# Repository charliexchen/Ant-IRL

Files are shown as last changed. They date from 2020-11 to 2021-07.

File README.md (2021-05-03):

# Ant-IRL

Ant-v2 (A.K.A Antony) is now a fairly standard RL task from the Open AI gym library. This project aims to achieve three goals:
* Build a physical robot in a similar configuration to Ant-v2
* Train Actor Critic on a physical environment with no simulation
* Use Haiku with JAX (https://github.com/deepmind/dm-haiku) on an end to end project

...in addition to staying sane over the third lock down in the UK.
 <p align="center">
   
 </p>
<p align="center"><i> <sub>Improvements in the robot's speed after training with AAC with experience replay in the simplified environment. Left: pretrained agent with some random noise in actions. Middle: agent after optimising for 33 episodes. Right: agent after optimising for 91 episodes</sub></i> </p>

## Building the Robot

<p align="center">
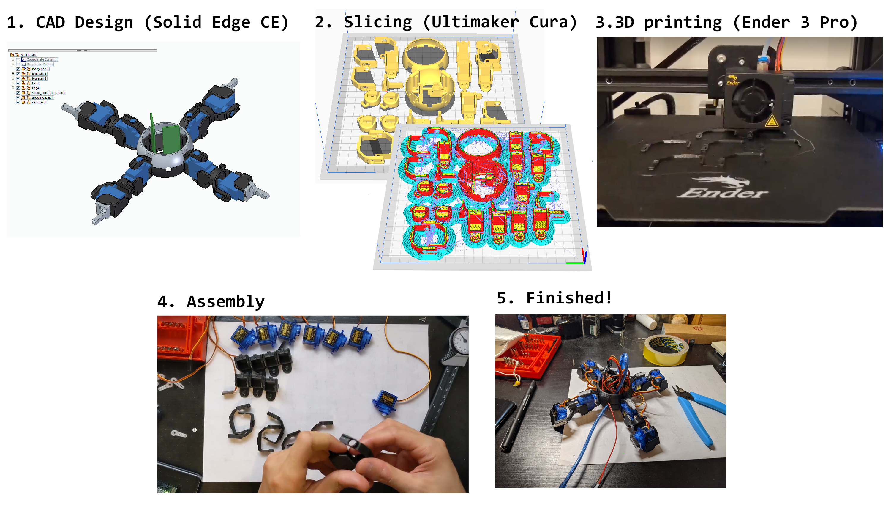
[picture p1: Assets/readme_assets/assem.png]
   
</p>

First, the robot was designed using Siemens Solid Edge CE (a powerful but free CAD software) and then 3D printed using my Creality Ender 3. The design consists of 8 servos in a similar configuration to Ant-v2 (albeit the forelegs are shorter to reduce the load on the tiny 9g servos). For control, I used an Arduino Nano which communicates with my desktop via USB serial and the servo controller via i2c. The position of each servo can be manipulated by sending two bytes of data.

For sensing, the Arduino is also connected to a gyro/accelerometer via i2c, which gives us acceleration, the gravity vector and Euler angles. Using the MPU-6050 sensor board's onboard DMP feature, it is not necessary to implement further noise reduction (such as Kalman/complement filters) for the sensors. Unfortunately, I eventually had to discard this data since it was just wasn't that helpful for my robot.

As a future upgrade, I have designed micro switch holders for the forelegs which will allow the robot to know if the legs have contacted the ground.

The robot runs on a 5v 2A DC power supply. Power and USB connection is maintained using 6 thin enamelled copper wires (usually used for electromagnets). This minimises any forces a stiff USB/power cable might impart onto the robot.

## Location Detection

The Robot's location and orientation relative to the environment is detected via the large aruco marker on top of the robot and markers on the corners of the environment. This was achieved with the aruco module in OpenCV. Under the correct lighting conditions, we can have the location of the robot over 99% of the time, and we can resort to last frame position or interpolating for any missing frames.

<p align="center">
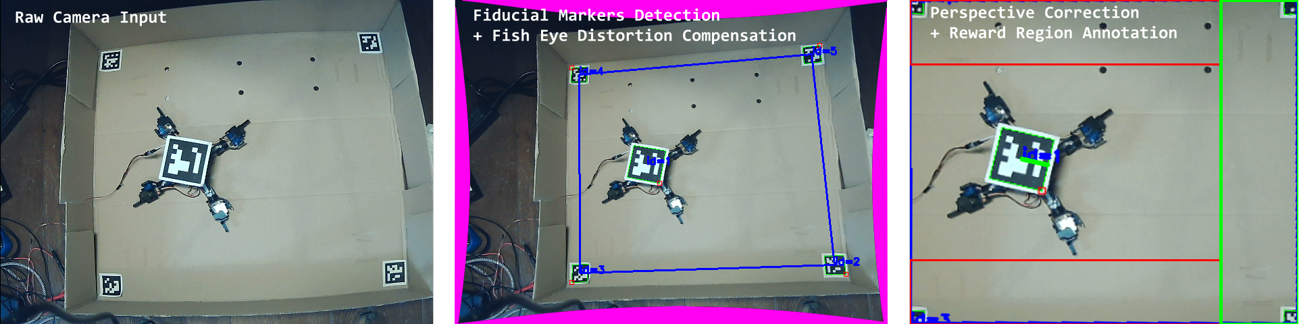
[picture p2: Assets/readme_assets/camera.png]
   
</p>
<p align="center"><i> <sub>Using OpenCV to correct the raw webcam input. Note the small amount of parallax if the camera is not directly overhead. This is usually small enough to not affect the results.</sub></i></p>

The capture setup consists of a cheap webcam on an angled tripod, pointing downwards. With the locations of the corners of the environment known, perspective and fisheye distortion can be corrected with standard OpenCV operations.

<p align="center">
  
</p>
<p align="center"><i> <sub>Camera setup and simple walk. Note the trailing wire connected to power and USB.</sub></i></p>

## Building an Environment

With the above setup, we can implement a state-action-reward loop, which forms the basis of the MDP. The robot would walk forth, collect data, train on that data using one's RL algorithm of choice, before resetting. 

* State consists of sensor inputs, absolute position, orientation, servo positions, creating a 22-dimensional vector (The simplified version of the environment removes sensor inputs, reducing the dimensionality to 12)
* Actions are 8 dimensional vectors representing either new absolute servo positions or deltas between the current position to the next.
* Reward is based on position, with +2 if it reaches the end of the field, -1 if it goes too far off the side and up to 1 for moving from left to right. The simplfied version of the envionment has the velocity dotted with the normalised orientation vector as the reward (essentially the forward speed).

A hand engineered walk cycle is also implemented. This was done for three reasons:
* Given a target and the robot's position, you can let the robot move up/down/left/right until it reached the target. This gives us a reliable method of resetting the robot's position after running an episode.
* We can collect data on this fixed walk cycle (in particular accelerometer/gyro data) in order to pretrain policiy/value functions.
* This makes room for lots of fun, future, non deep-learning projects. I can simply map the commands to keyboard/some other controller, and we basically have a walker which can reliably move in any direction.

<p align="center">
  
</p>
<p align="center"><i> <sub>Walking to specified locations by combining the camera and the hand engineered gait. This is used to reset the environment.</sub></i></p>

## Implementing and Running AAC

I implemented Advantage Actor-Critic using JAX and Haiku. This was a fun framework to use since it is a lot more flexible compared to the others I've tried in the past, such as Keras. Almost any numpy operation can be accelerated, vectorised or differentiated, so I can see this handling more unconventional architectures much more gracefully, even though the overall feature gap isn't huge compared to other frameworks. For example, I especially liked how for autograd, we use grad which is treated like a function operator much like how gradients are represented mathematically.

I made the predictor and AAC class as generic as possible for future projects, and tested that it works on CartPole.

Since this is a physical environment with one agent, we are very data constrained. As such, I first ran a number of episodes using the fixed walk cycle. We collect this data and then use it to pretrain the value function and an actor based on a fixed gait. We then use the above AAC implementation along with experience replay to improve the agent. The initial data also allows for some hyperparameter selection, which was done with a simple random search. 

 <p align="center">
     
 </p>
<p align="center"><i> <sub>Running multiple episodes with fixed agent in the environment to collect training data. Red rectangles terminate with negative reward, green with positive reward. After an episode, the agent returns to the red circle to reset the environment. Note the aruco markers used to ensure consistent perspective in the corners of the environment. </sub></i> </p>

Other things to note about the AAC implementation:
* The environment runs at 30fps (bounded by the frame rate of the camera). This can be downsampled by simply issuing a new action only every x frames. This can give the NNs a longer effective time horizon, in addition to making the setup less sensitive to latency in the camera, sensors and servo controller.
* The problem can be further simplified by imposing symmetries into the robot's actor, though this does remove the robot's ability to turn.
* In order to learn a continuous action space, the actor simply returns the mean values of a normal distribution. The variance is fixed for exploration, but it can also be the output of the actor.

<p float="left" align="center">
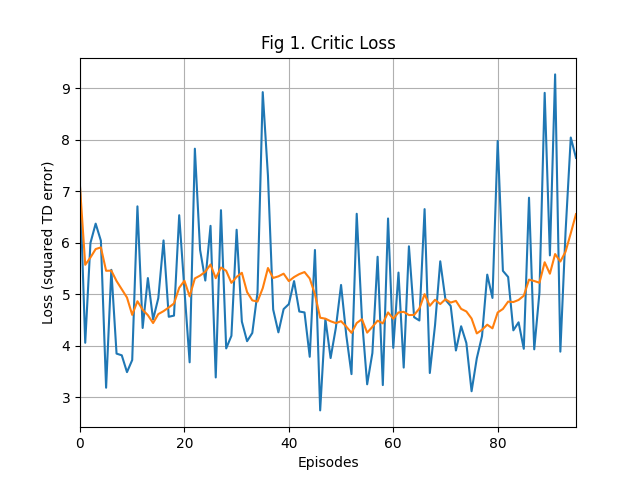
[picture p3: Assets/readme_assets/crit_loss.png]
  
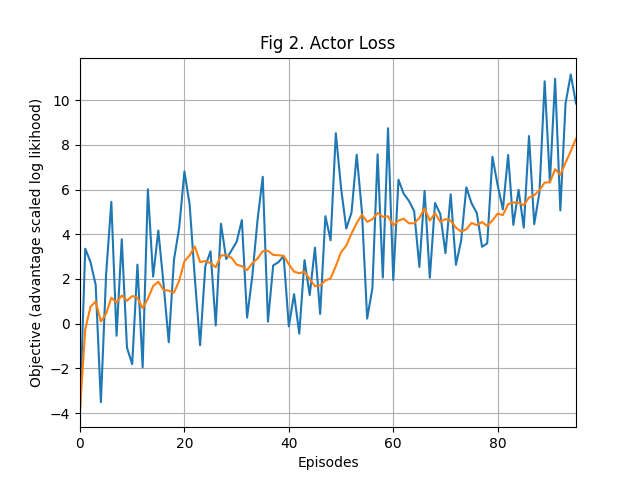
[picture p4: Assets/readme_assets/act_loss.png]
 
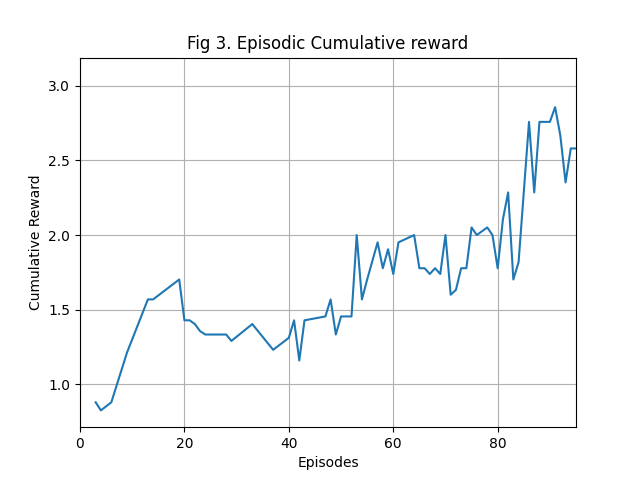
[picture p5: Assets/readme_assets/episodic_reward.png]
 
</p>
<p align="center"><i> <sub>Fig 1: loss function at each episode of the value critic. Given AAC is on-policy, we can expect this value to not go down as long as the policy has not converged. Fig 2: objective of the actor policy. This is the log-likelihood scaled advantage, and so we expect it to go up as the agent improves. Fig 3: Episodic cumulative reward -- the agent is moving faster as the policy improves.</sub></i> </p>

Tuning RL algorithms is hard. To make my life easier, I followed the best some best practices:
* Normalise the input and ouput of the NNs so the values across the layers are of similar magnitude
* Offline training/hyperparameter tuning uses train/dev/test sets to prevent overfitting
* Experiment configurations are separated into config files
* End to end tests for all major components in order to ensure correctness

## References
Main papers I consulted:
* [Challenges of Real-World Reinforcement Learning](https://arxiv.org/abs/1904.12901) -- This is a deepmind paper which gave a high level overview of the kind of problems I'm going to encounter, and served as a good jumping off point.
* [Automated DeepReinforcement Learning Environment for Hardware of a Modular Legged Robot](https://ieeexplore.ieee.org/document/8442201) -- A Disney research paper on getting various configurations to walk using DDPG and TRPO on a modular walking robot. Pretty cool, and gave me an idea about possible RL algorithm candidates. This paper actually trained the agent starting with one leg and increasing the number as legs as you go.
* [Optimizing walking of a humanoid robot using reinforcement learning](https://www.researchgate.net/publication/267024754_Reinforcement_Learning_with_Experience_Replay_for_Model-Free_Humanoid_Walking_Optimization) -- A masters thesis from university of warsaw using AAC. My architecture ended up being pretty similar to this one.
* [RealAnt: An Open-Source Low-Cost Quadruped for Research in Real-World Reinforcement Learning](https://arxiv.org/abs/2011.03085) -- A paper which also builds a open source robot, and trains some gaits on it. This was published days after I had done most of CAD work, so that was a little annoying. However, this design used much more expensive servos (each servo cost more than my robot put together) which has inbuilt sensors, superior control and full 360 rotation, and I think that might be worth investing in...
## Parts List
* [WebCam](https://www.amazon.co.uk/gp/product/B08CXV11MX/ref=ppx_yo_dt_b_asin_title_o00_s00?ie=UTF8&psc=1) -- Basically any webcam will do, though I ended up using this one side it comes with a standard standard 1/4-20 UNC thread for use on a tripod, in addition to a hinge and ball mount. These features are fairly common in other webcams though, so don't worry about getting the exact one. If you have a good camera which can be directly connected to PC, there's nothing really stopping you from using that -- just make sure that the latency low and you can detect the fiducial markers.
* [Arduino Nano](https://www.amazon.co.uk/ELEGOO-Arduino-board-ATmega328P-compatible/dp/B072BMYZ18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) -- Standard arduino. [There are lots of tutorials online for using these](https://store.arduino.cc/).
* [PCA9685 Servo Controller](https://www.amazon.co.uk/TeOhk-Channel-Interface-Controller-Raspberry/dp/B07RVJRQX1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) -- Interfaces with arduino with i2c and connects to external power.
* [MPU-6050 Sensor Board](https://www.amazon.co.uk/Neuftech%C2%AE-MPU-6050-3-gyroscope-accelerometer-crafting/dp/B00PIMRJX6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) -- Accelerometer, gyro and temperature sensor on a single board which can then communicate with i2c. Gyros are very accurate, but its values need to be integrated in order to get angular position, resulting in drift. Accelerometers don't have problems in drift, but are often really noisy. It is possible to combine data from both sensors in order to get the best of both worlds, and the DMP feature on these boards mean you don't have to write the complement filter yourself. Tutorial on how to get the DMP working can be found [here](https://maker.pro/arduino/tutorial/how-to-interface-arduino-and-the-mpu-6050-sensor), though personally I did discard the data here since it wasn't super helpful.
* [Tower Pro SG90 Servos](https://www.amazon.co.uk/gp/product/B07LBS7WYZ/ref=ppx_yo_dt_b_asin_title_o03_s00?ie=UTF8&psc=1) -- Super cheap 9g servos used in model aircraft. I recommend looking at some more expensive ones with the same dimensions however, since these were pretty imprecise.
* [SUNLU PLA filament](https://www.amazon.co.uk/gp/product/B07TMKGGS3/ref=ppx_yo_dt_b_asin_title_o00_s00?ie=UTF8&psc=1) -- I used this black filament, but PLA is so forgiving a plastic to print it really doesn't matter which brand you use.
* [0.2mm Enamelled copper wire](https://www.ebay.co.uk/itm/143728062658?ssPageName=STRK%3AMEBIDX%3AIT&_trksid=p2060353.m2749.l2649) -- Usually used for making electromagnets. I used this to make a long flexible cable with 6 wires, 4 for USB, and 2 for powering the servos. Some light soldering is needed here.
* [5v 2a power supply](https://www.amazon.co.uk/gp/product/B08DXX6LGG/ref=ppx_yo_dt_b_asin_title_o06_s00?ie=UTF8&psc=1) -- Used to power the servos. You can power one or two servos directly with the arduino, but you'll need an external power supply if you want to power more -- drawing too much current will damage the arduino. Be careful with these -- whilst they're not going to burn your house down, they're surprisingly expensive compared to the rest of the project and will fry themselves if shorted. If you forsee that you're going to be doing a lot of electrionic projects, I recommend getting one of these [variable DC power supplies](https://www.amazon.co.uk/gp/product/B08HQG9D56/ref=ppx_yo_dt_b_asin_title_o02_s00?ie=UTF8&psc=1), since they're much more flexible and is current limited, protecting it against shorts.
<p align="center">
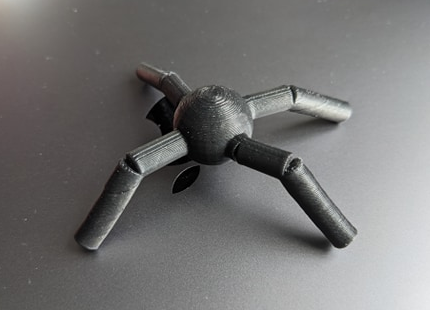
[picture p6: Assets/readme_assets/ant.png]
     
 </p>
 <p align="center"><i> <sub>You've made it to the end! Thank you for reading! </sub></i> </p>

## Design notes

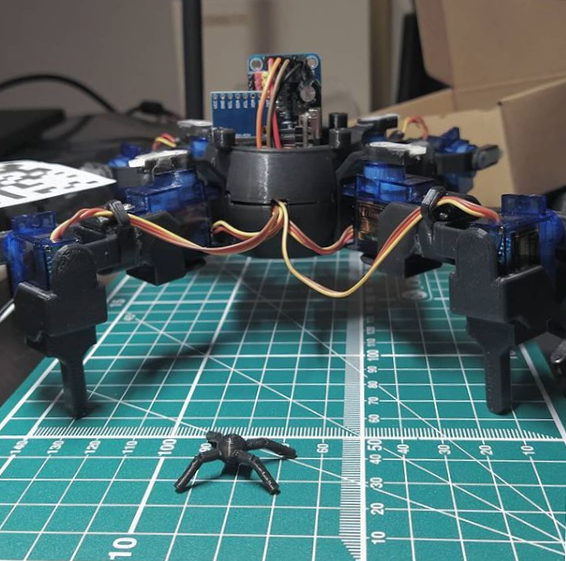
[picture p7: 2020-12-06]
Assets/readme_assets/ant_irl.png

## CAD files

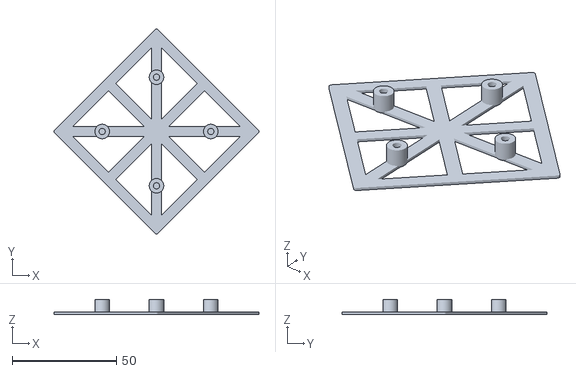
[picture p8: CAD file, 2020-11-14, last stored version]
Parts/qr_holder.stl
98.2 x 98.2 x 7.00

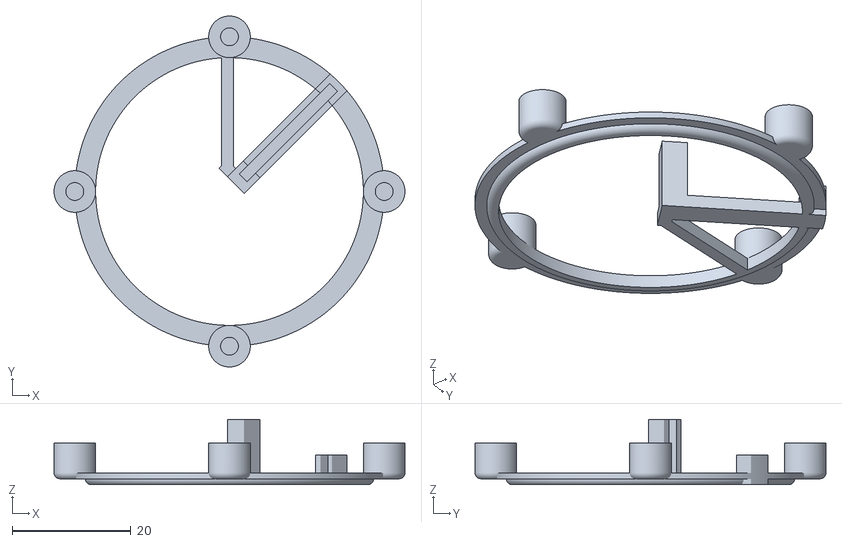
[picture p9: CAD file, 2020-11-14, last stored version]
Parts/modular_holder.stl
59.0 x 59.0 x 11.0

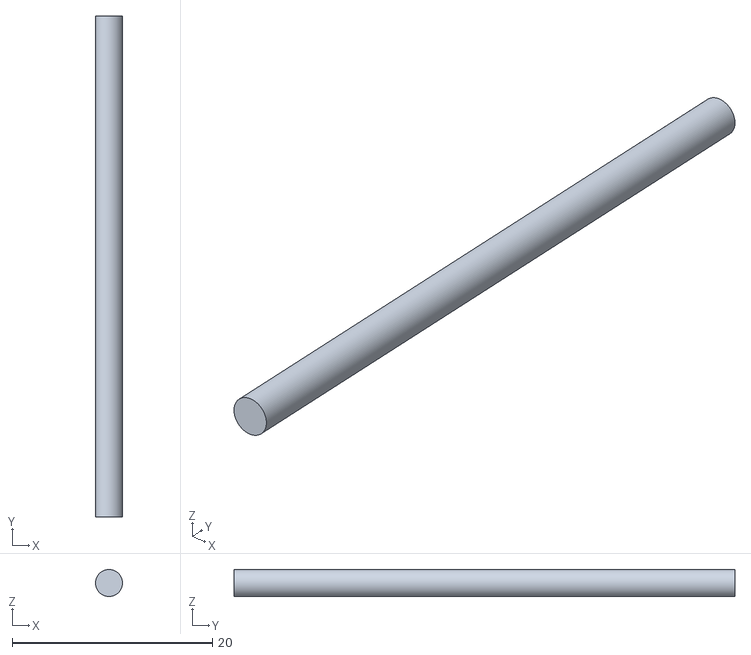
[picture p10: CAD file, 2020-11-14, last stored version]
Parts/rod.stl
2.70 x 50.0 x 2.70

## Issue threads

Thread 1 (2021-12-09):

error opening ant.asm

wegesdal, 2021-12-09:
feet.par, joint.asm, thigh.par missing from assets folder. Is ant.asm based on a previous directory structure? joint.asm and thigh.par have path outside project folder.

charliexchen, 2021-12-09:
Heya -- yeah, I rejigged the file structure a little since it was a little all over the place before and this seems to have broken the .asm files.

I've since moved away from Solid Edge for Fusion 360 on my new desktop, so I can't fix this this at the moment. However,
as a temporary measure but you should be able to use Solid Edge to point the directories to the correct positions.

wegesdal, 2021-12-10:
Sounds good. It looks like joint and thigh are missing from the parts folder unless those have been renamed. The path was to desktop instead of parts folder. I am going to try and put one together. My final project for AI was testing Soft-Actor-Critic in gym and I was interested to build my own Ant.

charliexchen, 2021-12-10:
Ah, I see.

charliexchen, 2021-12-11:
Heya, I'm terribly sorry --  I had a look at my backups today, and I'm afraid that file actually lives on a different computer which I currently don't have access to.

If you really need the part ASAP, thigh.par should be quite easy to design. I've highlighted the part of the robot CAD image it refers to.
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

This part is literally just a cylinder with a rectangular hole on each end. The two holes are perpendicular to eachother. On the bracket.par and outer bracket.par files, there is a rectangle which aligns with these holes as you glue the parts together.

wegesdal, 2021-12-11:
I am using mujoco gym for my project I was going to build the robot to extend my learning so I don't have a deadline.

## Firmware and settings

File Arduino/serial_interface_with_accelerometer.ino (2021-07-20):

#include "I2Cdev.h"
#include "MPU6050_6Axis_MotionApps20.h"
#if I2CDEV_IMPLEMENTATION == I2CDEV_ARDUINO_WIRE
#include "Wire.h"
#endif


#include <Wire.h>
#include <Adafruit_PWMServoDriver.h>


Adafruit_PWMServoDriver pwm = Adafruit_PWMServoDriver();
int incomingByte = 0;    // for incoming serial data
int currentCommands[8] = {1500, 1500, 1500, 1500, 1500, 1500, 1500, 1500}; // initial servo positions
int servoPositionOffset = 8;

int maxPulse = 2400;
int minPulse = 600;

unsigned int raw_command = 0;
#define SERVO_FREQ 50 // Analog servos run at ~50 Hz updates

int granularity = 1;


MPU6050 mpu;

#define INTERRUPT_PIN 2  // use pin 2 on Arduino Uno & most boards
#define LED_PIN 13 // (Arduino is 13, Teensy is 11, Teensy++ is 6)
bool blinkState = false;

// MPU control/status vars
bool dmpReady = false;  // set true if DMP init was successful
uint8_t mpuIntStatus;   // holds actual interrupt status byte from MPU
uint8_t devStatus;      // return status after each device operation (0 = success, !0 = error)
uint16_t packetSize;    // expected DMP packet size (default is 42 bytes)
uint16_t fifoCount;     // count of all bytes currently in FIFO
uint8_t fifoBuffer[64]; // FIFO storage buffer

// orientation/motion vars
Quaternion q;           // [w, x, y, z]         quaternion container
VectorInt16 aa;         // [x, y, z]            accel sensor measurements
VectorInt16 aaReal;     // [x, y, z]            gravity-free accel sensor measurements
VectorInt16 aaWorld;    // [x, y, z]            world-frame accel sensor measurements
VectorFloat gravity;    // [x, y, z]            gravity vector
float euler[3];         // [psi, theta, phi]    Euler angle container
float ypr[3];           // [yaw, pitch, roll]   yaw/pitch/roll container and gravity vector

typedef struct {
  float qw;
  float qx;
  float qy;
  float qz;
  float y;
  float p;
  float r;
  float gx;
  float gy;
  float gz;
  float ed = 99999999.9;
} __attribute__((__packed__))data_packet_t;

data_packet_t dp;

volatile bool mpuInterrupt = false;     // indicates whether MPU interrupt pin has gone high
void dmpDataReady() {
  mpuInterrupt = true;
}

void setup() {

  Serial.begin(9600);    // opens serial port, sets data rate to 9600 bps

  pwm.begin();
  pwm.setOscillatorFrequency(27000000);
  pwm.setPWMFreq(SERVO_FREQ);  // Analog servos run at ~50 Hz updates

  // join I2C bus (I2Cdev library doesn't do this automatically)
#if I2CDEV_IMPLEMENTATION == I2CDEV_ARDUINO_WIRE
  Wire.begin();
  Wire.setClock(400000); // 400kHz I2C clock. Comment this line if having compilation difficulties
#elif I2CDEV_IMPLEMENTATION == I2CDEV_BUILTIN_FASTWIRE
  Fastwire::setup(400, true);
#endif
  while (!Serial); // wait for Leonardo enumeration, others continue immediately
  Serial.println(F("Initializing I2C devices..."));
  mpu.initialize();
  pinMode(INTERRUPT_PIN, INPUT);
  Serial.println(F("Testing device connections..."));
  Serial.println(mpu.testConnection() ? F("MPU6050 connection successful") : F("MPU6050 connection failed"));
  Serial.println(F("Initializing DMP..."));
  devStatus = mpu.dmpInitialize();
  if (devStatus == 0) {
    // Calibration Time: generate offsets and calibrate our MPU6050
    mpu.CalibrateAccel(6);
    mpu.CalibrateGyro(6);
    mpu.PrintActiveOffsets();
    // turn on the DMP, now that it's ready
    Serial.println(F("Enabling DMP..."));
    mpu.setDMPEnabled(true);

    // enable Arduino interrupt detection
    Serial.print(F("Enabling interrupt detection (Arduino external interrupt "));
    Serial.print(digitalPinToInterrupt(INTERRUPT_PIN));
    Serial.println(F(")..."));
    attachInterrupt(digitalPinToInterrupt(INTERRUPT_PIN), dmpDataReady, RISING);
    mpuIntStatus = mpu.getIntStatus();

    // set our DMP Ready flag so the main loop() function knows it's okay to use it
    Serial.println(F("DMP ready! Waiting for first interrupt..."));
    dmpReady = true;

    // get expected DMP packet size for later comparison
    packetSize = mpu.dmpGetFIFOPacketSize();
  } else {
    // ERROR!
    // 1 = initial memory load failed
    // 2 = DMP configuration updates failed
    // (if it's going to break, usually the code will be 1)
    Serial.print(F("DMP Initialization failed (code "));
    Serial.print(devStatus);
    Serial.println(F(")"));
  }

  // configure LED for output
  pinMode(LED_PIN, OUTPUT);
  delay(500);
  Serial.println("Ant Ready!");
   delay(500);
}


void loop() {
  if (Serial.available() > 0) {
    while (Serial.available() > 0) {
      incomingByte = Serial.read();
      raw_command = (raw_command << 7) | (incomingByte & 127);
      bool is_last_bit = (incomingByte & 128) == 128;
      if (is_last_bit) {
        int servo_id = raw_command & 7;
        int servo_pos = (raw_command >> 3) + minPulse;
        if (servo_pos > maxPulse) {
          servo_pos = maxPulse;
        }
        currentCommands[servo_id] = servo_pos;
        raw_command = 0;
      }
    }
  }
  for (int i = 0; i < 8; i++) {
    uint16_t raw_servo_id = i + servoPositionOffset;
    uint16_t raw_ms_command = (currentCommands[i] * granularity);
    pwm.writeMicroseconds(raw_servo_id, raw_ms_command);
  }
  if (mpu.dmpGetCurrentFIFOPacket(fifoBuffer)) {
    mpu.dmpGetQuaternion(&q, fifoBuffer);
    mpu.dmpGetEuler(euler, &q);
    mpu.dmpGetGravity(&gravity, &q);
    mpu.dmpGetYawPitchRoll(ypr, &q, &gravity);
    mpu.dmpGetAccel(&aa, fifoBuffer);
    mpu.dmpGetLinearAccel(&aaReal, &aa, &gravity);
    mpu.dmpGetLinearAccelInWorld(&aaWorld, &aaReal, &q);
    dp.qw = q.w;
    dp.qx = q.x;
    dp.qy = q.y;
    dp.qz = q.z;
    dp.y = ypr[0];
    dp.p = ypr[1];
    dp.r = ypr[2];
    dp.gx = gravity.x;
    dp.gy = gravity.y;
    dp.gz = gravity.z;
    Serial.write((byte*)&dp, sizeof(dp));
  }
  delay(5);

  if (!dmpReady) {
    return;
  }
}

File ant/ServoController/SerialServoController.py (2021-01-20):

#!/usr/bin/python
import numpy as np
import serial
import struct
import time

from ServoController.ServoIDConfig import (
    MAX_PULSE,
    MIN_PULSE,
    MAX_SERVO_COUNT,
    is_inverted,
)
from ServoController.WalktCycleConfigParser import WalkCycle


class SerialServoController:
    """
    Class which sends and receives commands to/from the arduino via pySerial. The Arduino parses the commands and moves
    the robot. We can parse the serial from the robot, and this way we can access the accelerometer data.
    """

    PULSE_GRANULARITY_16BIT_8SERVOS = 1
    DEFAULT_SEPARATOR = [0, 252, 127, 63]  # 100000000.0 float value
    CALIBRATION = [0, 0, 0, 0, -50, -100, -100, 0]

    def __init__(
        self,
        port: str,
        baudrate: int = 9600,
        input_data_format: str = "fffffffffff",
        reset_threshold=50,
    ):
        print("Connecting to Antony via serial...")
        self.port = port
        self.baudrate = baudrate
        self.ser = serial.Serial(port, baudrate=baudrate)
        self.ser.timeout = 0.024
        self.current_command = {
            servo_id: self.centre() for servo_id in range(MAX_SERVO_COUNT)
        }
        self.struct_format = input_data_format
        self.struct_size = struct.calcsize(input_data_format)
        self.buffer = []
        self.latest = []
        self.reset_threshold = reset_threshold
        self.reset_counter = 0
        self.ready = False

        print("Waiting for Antony to respond...")
        self.wait_for_connection()

    @staticmethod
    def _get_16bit_servo_command(servo_id: int, position: int) -> bytes:
        """
        Converts a servo command pair into two bytes, which can then be sent to the robot
        :param servo_id
        :param position: servo command based on PWM
        :return: two bytes which the arduino can parse and act on.
        """
        calibrated_pos = position + SerialServoController.CALIBRATION[servo_id]
        calibrated_pos = np.clip(calibrated_pos, MIN_PULSE, MAX_PULSE)
        assert servo_id < MAX_SERVO_COUNT, "Error -- Servo ID exceeds max servo count"
        discretized_position = int(
            (calibrated_pos - MIN_PULSE)
            / SerialServoController.PULSE_GRANULARITY_16BIT_8SERVOS
        )
        command = (discretized_position << 3) + servo_id
        assert command >> 14 == 0, "Error command exceeds 16 bits"
        second_byte = (command & 127) | 128
        first_byte = (command >> 7) & 127
        return bytes([first_byte, second_byte])

    def _get_command_from_normalised_positions(self, servo_id, normalised_position):
        """
        Converts float from +/-1 to servo command. +1 means legs move forward, and feet moves down. This makes it easier
        for the ML models later on
        :param servo_id
        :param normalised_position: position of servo from +/-1, raw ML model output
        :return: servo command based on PWM
        """
        if is_inverted(servo_id):
            normalised_position *= -1
        return self.centre() + int(normalised_position * ((MAX_PULSE - MIN_PULSE) / 2))

    @staticmethod
    def centre() -> int:
        return int((MAX_PULSE + MIN_PULSE) / 2)

    def send(self, commands):
        """
        Sends the command to the robot.
        :param commands: dict of servo to position
        """
        if not self.ready:
            return
        for servo_id in commands:
            self.current_command[
                servo_id
            ] = self._get_command_from_normalised_positions(
                servo_id, commands[servo_id]
            )
        commands = [
            self._get_16bit_servo_command(servo_id, position)
            for servo_id, position in self.current_command.items()
        ]
        for command in commands:
            self.ser.write(command)

    def send_centre_command(self):
        self.send({servo_id: 0 for servo_id in range(MAX_SERVO_COUNT)})

    def send_idle_command(self):
        """
        Sends a single command which puts the robot to the idle position.
        """
        self.send({0: 0, 1: 0, 2: 0, 3: 0, 4: 0.9, 5: 0.9, 6: 0.9, 7: 0.9})

    def send_pack_up_command(self):
        """
        Sends a single command which makes the robot curl up into a ball so I can pack it snugly in a box.
        """
        self.send(
            {0: -1.0, 1: 1.0, 2: -1.0, 3: 1.0, 4: -1.0, 5: -1.0, 6: -1.0, 7: -1.0}
        )

    def get_data_if_ready(self):
        """
        Takes the raw data from the arduino, and parses it so we can access the sensor information. The loaded data is
        stored in self.latest, so is no data is received we just send the same as the last frame.
        :return: parsed struct based on input_data_format, None if the robot has frozen or the system is not yet ready.
        """
        serial_data = self.ser.read_all()
        if serial_data == b"Ant Ready!\r\n":
            print("Ready!")
            self.ready = True
        if not self.ready:
            return
        if self._detect_frozen_state(serial_data):
            return
        self.buffer.extend(serial_data)
        self._update_serial_data()
        if len(self.latest) == self.struct_size:
            return struct.unpack(self.struct_format, bytes(self.latest))

    def _detect_frozen_state(self, serial_data):
        """
        Checks if the accelerometer is returning nothing for too long, and resets the connection if it happens.
        :return: Boolean if frozen state was detected
        """
        if len(serial_data) == 0:
            self.reset_counter += 1
            if self.reset_counter > self.reset_threshold:
                print("Robot is frozen -- resetting the connection...")
                self.reset_connection()
                return True
        else:
            self.reset_counter = 0
        return False

    def _update_serial_data(self):
        """
        Ugly piece of code which splits the data in the buffer based on the separator bytes and saves it into
        self.latest. Since the arduino is sending raw bytes, we can't have a dedicated separator byte, so we have a
        sequence to reduce the prob of a collision.
        :return: void
        """
        if not self.ready:
            return
        i = 0
        if len(self.buffer) < self.struct_size:
            return
        while i < len(self.buffer):
            matched = True
            for j, sub_ele in enumerate(self.DEFAULT_SEPARATOR):
                if i + j >= len(self.buffer) or sub_ele != self.buffer[i + j]:
                    matched = False
                break
            if matched:
                if len(self.buffer) - i >= self.struct_size:
                    self.latest = self.buffer[i : i + self.struct_size]
                    i += self.struct_size
                else:
                    self.buffer = self.buffer[i:]
                    break
            else:
                i += 1

    def close_ports(self):
        self.ser.close()
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

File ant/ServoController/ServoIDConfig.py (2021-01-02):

from enum import Enum
from typing import Union

"""
Bunch of constants and utils relating to servo commands
"""

MAX_PULSE = 2400
MIN_PULSE = 600
MAX_SERVO_COUNT = 8


class Servos(Enum):
    FRONT_RIGHT_HIP = "front_right_hip"
    FRONT_LEFT_HIP = "front_left_hip"
    BACK_LEFT_HIP = "back_left_hip"
    BACK_RIGHT_HIP = "back_right_hip"
    FRONT_RIGHT_LEG = "front_right_leg"
    FRONT_LEFT_LEG = "front_left_leg"
    BACK_LEFT_LEG = "back_left_leg"
    BACK_RIGHT_LEG = "back_right_leg"


INVERTED_SERVOS = {
    Servos.FRONT_RIGHT_HIP,
    Servos.BACK_RIGHT_HIP,
    Servos.FRONT_RIGHT_LEG,
    Servos.BACK_LEFT_LEG,
}

SPEED_DEPENDENT_SERVOS = {
    Servos.FRONT_RIGHT_HIP,
    Servos.BACK_RIGHT_HIP,
    Servos.BACK_LEFT_HIP,
    Servos.FRONT_LEFT_HIP,
}

SERVO_ENUM_TO_ID_MAP = {
    "front_right_hip": 0,
    "front_left_hip": 1,
    "back_left_hip": 2,
    "back_right_hip": 3,
    "front_right_leg": 4,
    "front_left_leg": 5,
    "back_left_leg": 6,
    "back_right_leg": 7,
}


def get_servo_id(servo: Union[Servos, str, int]) -> int:
    if type(servo) is int:
        return servo
    if servo in SERVO_ENUM_TO_ID_MAP:
        return SERVO_ENUM_TO_ID_MAP[servo]
    try:
        return SERVO_ENUM_TO_ID_MAP[servo.value]
    except AttributeError:
        return None


INVERTED_SERVO_IDS = {get_servo_id(servo) for servo in INVERTED_SERVOS}
SPEED_DEPENDENT_SERVO_IDS = {get_servo_id(servo) for servo in SPEED_DEPENDENT_SERVOS}


def is_inverted(servo: Union[int, Servos]) -> bool:
    return servo in INVERTED_SERVO_IDS or servo in INVERTED_SERVOS


def is_speed_dependent(servo: Union[int, Servos]) -> bool:
    return servo in SPEED_DEPENDENT_SERVO_IDS or servo in SPEED_DEPENDENT_SERVOS

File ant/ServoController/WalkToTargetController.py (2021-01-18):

import cv2
import numpy as np

from LocationCamera.AntDetectorCamera import AntDetectorCamera
from ServoController.SerialServoController import SerialServoController
from ServoController.WalktCycleConfigParser import (
    UnifiedFixedWalkController,
    WalkCommand,
)


class WalkToTargetController:
    """
    Combines AntDetectorCamera, SerialServoController and UnifiedFixedWalkController so we can have a simple feedback
    loop of the robot walking to a point on the screen using fixed walk cycles. This will be used to reset the
    environment and such
    """

    ANGLE_TOLERANCE = 0.3  # Number of radians to target before stopping
    POSITION_TOLERANCE = 20  # Number of pixels to target before stopping

    def __init__(self, port="/dev/ttyUSB0", speed=0.3, window_name="Ant Location"):
        self.unified_walk_controller = UnifiedFixedWalkController(speed=speed)
        self.servo_controller = SerialServoController(port)
        self.locator = AntDetectorCamera()
        self.window_name = window_name

        self.frame = None
        self.command = WalkCommand.IDLE
        self.serial_command = None
        self.set_mouse_callback()

    def set_mouse_callback(self):
        """
        We have to assign the mouse handler to the window so open CV would let us capture mouse events
        """
        cv2.namedWindow(self.window_name)
        cv2.setMouseCallback(
            self.window_name, self.locator.initialize_mouse_handler, self.locator
        )

    def align_orientation_command(self, orientation, target_orientation=np.pi / 2):
        if orientation is None:
            return WalkCommand.IDLE
        discrepancy = orientation - target_orientation
        if discrepancy > np.pi:
            discrepancy -= np.pi * 2
        elif discrepancy < -np.pi:
            discrepancy += np.pi * 2
        if discrepancy > self.ANGLE_TOLERANCE / 2:
            return WalkCommand.RIGHT_TURN
        elif discrepancy < -self.ANGLE_TOLERANCE / 2:
            return WalkCommand.LEFT_TURN

    def align_position_to_target_command(self, position, orientation, target):
        """
        Determines the command we should send based on the current state of the environment and the target. This doesn't
        need to be sophisticated, since it will just be used to reset the env.

        Robot prioritises aligning the orientation to the left. We want to minimise the robot turning, in order to
        reduce the chance of the robot getting tangled in the cables (it was really fiddly to solder and I do NOT want
        tear it apart). Then the robot tries to align the vertical, followed by the horizontal position.
        :param position:
        :param orientation:
        :param target:
        :return: WalkCommand which will help get to target
        """
        if target is None:
            return WalkCommand.IDLE
        orientation_command = self.align_orientation_command(orientation)
        if orientation_command is not None:
            return orientation_command
        position_discrepancy = position - target

        if np.linalg.norm(position_discrepancy) > 100:

            position_tolerance = self.POSITION_TOLERANCE * 2
        else:
            position_tolerance = self.POSITION_TOLERANCE

        if (
            abs(position_discrepancy[1]) > position_tolerance
        ):  # align y coordinate first
            if position_discrepancy[1] < 0:
                return WalkCommand.RIGHT
            else:
                return WalkCommand.LEFT

        elif abs(position_discrepancy[0]) > position_tolerance:
            if position_discrepancy[0] > 0:
                return WalkCommand.BACK
            else:
                return WalkCommand.FORWARD
        else:
            return WalkCommand.IDLE

    def send_serial_command(self, position, orientation, target):
        self.command = self.align_position_to_target_command(
            position, orientation, target
        )
        self.serial_command = self.unified_walk_controller.get_next_step(self.command)
        self.servo_controller.send(
            {id: com for id, com in enumerate(self.serial_command)}
        )

    def go_to_target(self, show_image=True):
        _, self.frame = self.locator.cap.read()
        annotated_frame = self.locator.correct_and_annotate_frame(self.frame)
        if show_image:
            cv2.imshow(self.window_name, annotated_frame)
        self.send_serial_command(
            self.locator.ant_centre,
            self.locator.ant_orientation_angle(),
            self.locator.target,
        )

    def end_session(self):
        self.locator.release_capture()
        self.servo_controller.close_ports()

    def get_target_normalised(self):
        return self.locator.target / max(
            self.locator.SCREEN_HEIGHT, self.locator.SCREEN_WIDTH
        )

    def set_target_normalised(self, normalised_target):
        self.locator.target = np.array(normalised_target) * max(
            self.locator.SCREEN_HEIGHT, self.locator.SCREEN_WIDTH
        )

    def get_normalised_position(self, show_image=True):
        _, self.frame = self.locator.cap.read()
        annotated_frame = self.locator.correct_and_annotate_frame(self.frame)
        if show_image:
            cv2.imshow(self.window_name, annotated_frame)
        return self.locator.ant_centre / max(
            self.locator.SCREEN_HEIGHT, self.locator.SCREEN_WIDTH
        )

    def get_orientation_vector(self):
        return self.locator.ant_orientation_vector

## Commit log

2020-11-12 uploading CAD files
    [ant.cfg, leg.cfg]
2020-11-14 added QR code holder
    [modular_holder.stl, qr_holder.stl, rod.stl]
2020-11-29 improved transition between different fixed cycle walks
    [ServoIDConfig.py, WalktCycleConfigParser.py]
2020-12-06 migrated to arUco markers, added calibration for camera view
2020-12-06 added class to handle the location detection and camera calibration
2020-12-17 arduino accelerometer
2020-12-18 now receives accelerometer data correctly
2020-12-19 Parse Accelerometer inputs
2021-01-18 implemented fixed cycle net
    [SerialServoController.py]
2021-01-20 reorganised asset folder
    [ant.cfg, leg.cfg, modular_holder.stl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]
2021-07-18 Stray test code in arduino
